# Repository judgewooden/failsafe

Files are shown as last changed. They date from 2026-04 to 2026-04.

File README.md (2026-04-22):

failsafe
========

## Synopsis

Failsafe is a project to determine if water is still flowing in a closed water loop for computer cooling. If the water is not flowing it will cut the power to the pump and computers. The computers are cooled with an external radiator and pump which is outside the house. Since these systems are far apart an Arduino monitors the flow to ensure that pumps will not run dry or there is no electric short when there is a water leak or an unknown incident.

Inside the house each computer is split into its own water loop via a manifold. Using flowmeters for each loop an http server display the flow-per-second so that the manifold valves could be adjusted manually. The data is also made available as JSON via rest for an external monitoring software solution running on a seperate Raspberry Pi.

## Code

As the project progressed more features got added:
- Arduino_email: Monitors a single water loop and send an email when the circuit breakers is activated.
- Arduino_dual: Monitors multiple water loops, expose data in rest for external monitoring and removed email.
- Arduino_nvram: Monitors multiple water loops and make it possible to service a computer. It stores the last config in nvram, so when it restarts it will remember what loops needs to be monitored.

## Motivation

The computers are on 24/7 and with water cooling things sometimes go wrong. But it was also an opportunity to learn more about hardware programming and the Arduino.

## Installation

Hardware:

- 1x Arduino
- 1x Arduino Ethernetboard (Duemilanova w/Atmega328)
- 3x water flow meters
- 1x 220v switch

## Circuits

- fritzing = logical circuit drawing
- picture = circuit board (With before pictures)

## Tests

There was several leaks over the years and the failsafe works.

## Example

Below is a sample screen of what you can control via the web server.

- In this example only two loops are active and only loop-0 is being monitored.
- Set minutes. Allows you to temporary disable monitoring. This is needed when you service the outside loop (radiator) or when you start the system. It will countdown and eventually reset to monitoring mode.
- Change ON/OFF per loop. This allows you to enable/disable monitoring per loop. Useful if you service a computer. The eeprom-code option allow you to save this setting into eeprom.

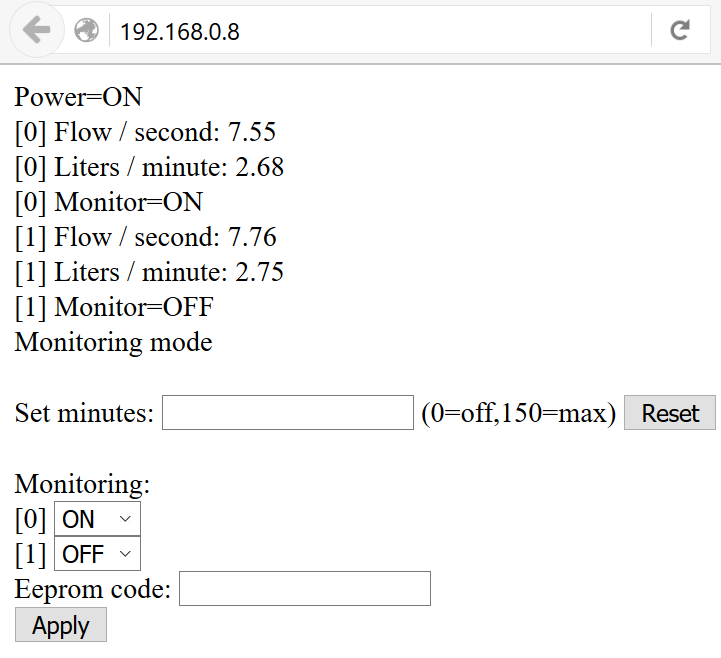
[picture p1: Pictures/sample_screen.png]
sample screen


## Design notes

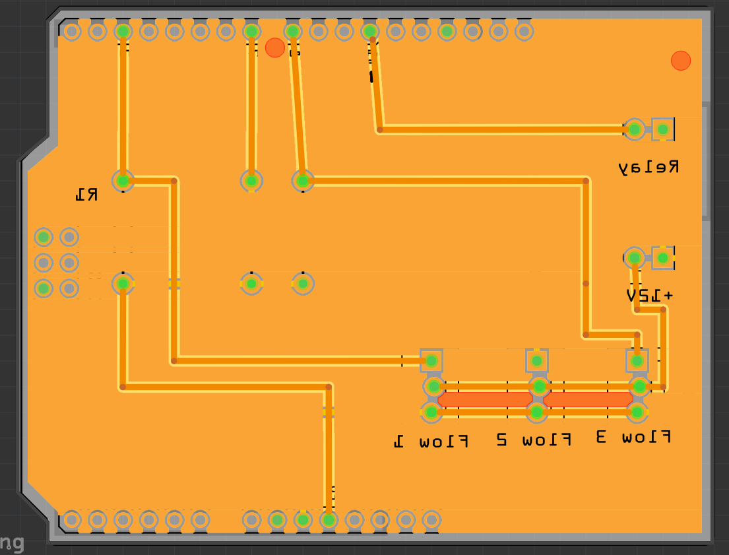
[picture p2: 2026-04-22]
Pictures/A_pcb_back.png

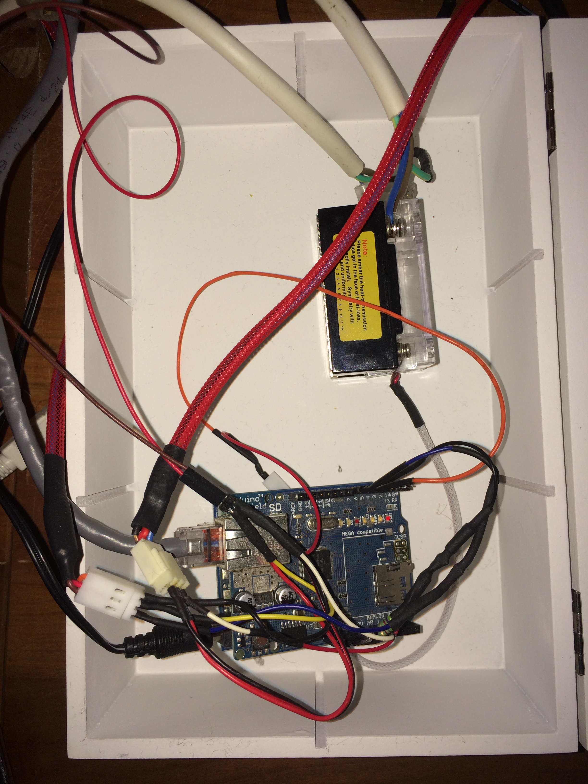
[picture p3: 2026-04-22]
Pictures/Two_circuits.jpg

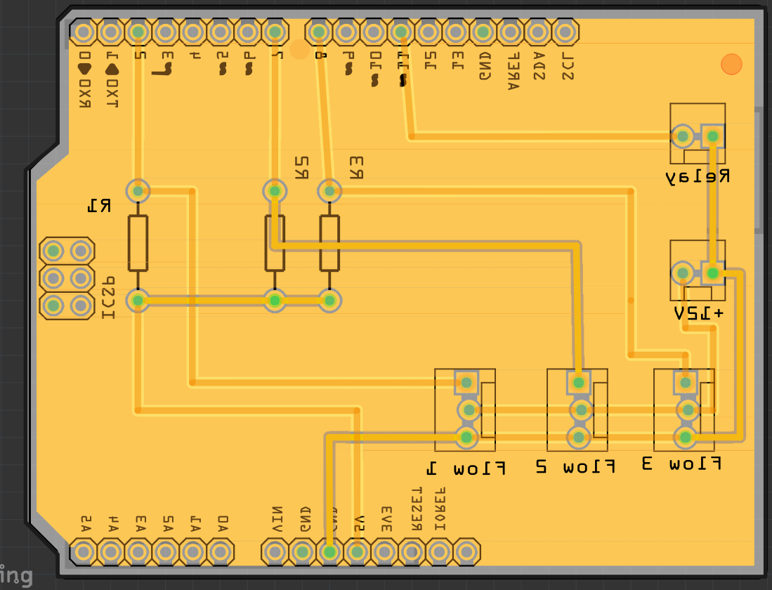
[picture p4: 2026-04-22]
Pictures/A_pcb_front.png

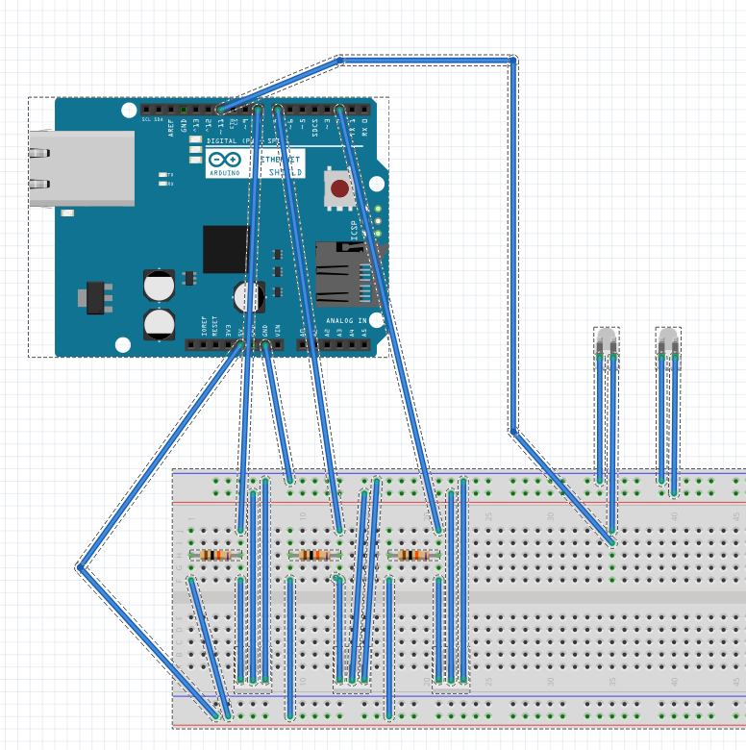
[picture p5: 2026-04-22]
Pictures/A_breadboard.png

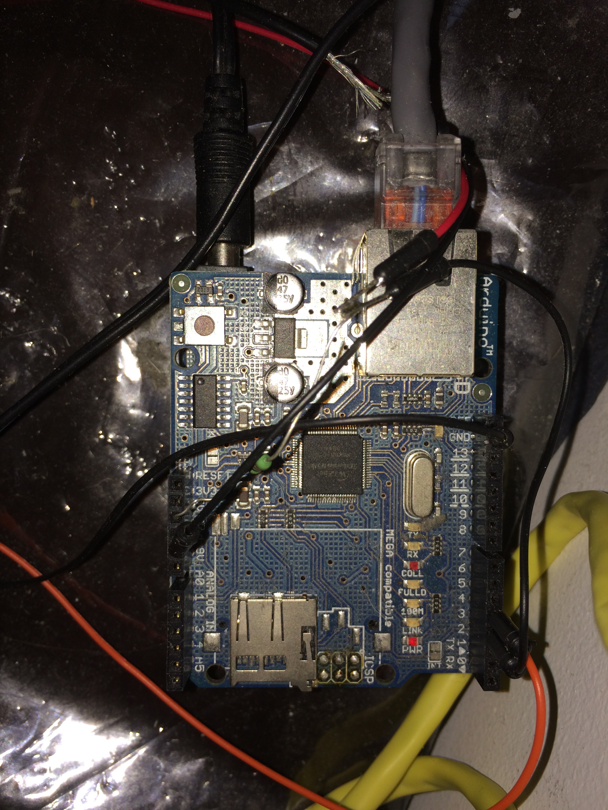
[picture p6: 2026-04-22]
Pictures/Single_circuit.jpg

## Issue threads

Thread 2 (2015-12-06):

When no flow, last readings is not updated

judgewooden, 2015-12-06:
Readings are not updated, where there is no flow. Although failsafe has been activated the web interface can still show the wrong last values

Closed 2016-02-14.

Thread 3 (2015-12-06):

Create a second flow meters to monitor

judgewooden, 2015-12-06:
First create an overflow failsafe with two reporting XML outputs and one website.

Later considering adding a failsafe OVERRIDE mode per sensor.

Closed 2016-02-14.

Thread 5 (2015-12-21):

Send a notification to server a httlp server on failsafe

judgewooden, 2015-12-21:
When the failsafe kicks in, sent a http GET message with parameters about the current status and config after the power is switched off.

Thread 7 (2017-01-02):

Issues with JSON array

judgewooden, 2017-01-02:
Sometime the array is not ending correct. Notice comma after last field in example below.

{"Power":1,"Loop":0,"Mode":2,"ValuesReset":0,"FlowPerSecond":3.08,"LitersPerSecond":1.09,"OverrideTime":0,"CurrentTime":3958098307,"data":[3958090244,3958090569,3958090892,3958091210,3958091533,3958091862,3958092185,3958092507,3958092830,3958093155,3958093483,3958093810,3958094132,3958094453,3958094789,3958095119,3958095442,3958095766,3958096129,3958096413,3958096741,3958097063,3958097385,3958097714,3958098038,]}

judgewooden, 2020-02-17:
It has now been running for 2 years. The error is only for users that extract the data as JSON. Unfortunately a user that extracts JSON needs to check for this comma, before parsing it.

Closed 2020-02-17.

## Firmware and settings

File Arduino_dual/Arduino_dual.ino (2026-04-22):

#include "Ethernet.h"
#include <SPI.h>

// Upload to Arduin Duemilanova w/ Atmega328

#define DEBUG 1

int debugflow = 1;                     // Are we debugging flow via serial interface
int debughttp = 1;                     // Are we debugging http via serial interfaces

const int numCircuits = 2;             // number of water sensors connected
const int numReadings = 25;            // number of pulses to check for flow calculation

int pin_input[] = {5, 7};              // On what pins are the water seonsors connected
double pulses_per_liter[] = {169,492};
                                       // Number of pulses per liter water
int pin_output = 6;                    // On what pin is the circuit breaker connected

long override_time= 120000;             // Give a 2 minute startup
int override_mode = 0;                  // Are we monitoring the flow
int Is_Power_On = 0;                    // Keep the state of the power breaker
int jsonresponse = 0;                   // Should I reply with JSON data on the HTML

int lastpulse[numCircuits];             // Was the last pulse high or low
unsigned long last_pulse_time[numCircuits];
                                        // When was the last pulse
unsigned long readings[numReadings][numCircuits];
                                        // Array to keep pin readings to calculate flow
int index[numCircuits];                 // keep track where we are in the Array
double Pulses_Per_Second[numCircuits];  // The calculated pulses per second
double Liter_per_minute[numCircuits];   // The calculated liters per minute
int valuesreset[numCircuits];           // Indicate if values are reset

unsigned long current_time;             // get the current system time
unsigned long timeout_millisecs = 5000; // Nr of miliseconds of no flow before activating circuit breakers

const double MilliPerSecond = 1000;     // a field to force caculcation as a double
unsigned long report_count = 0;         // the last time that a caulcation for flow was ade
int report_interval = 1000;             // Nr of miliseconds to calculate flow numbers

// Ethernet library configuration
byte mac[] = {
  0xDE, 0xAD, 0xBE, 0xEF, 0xFE, 0xED }; //physical mac address
byte ip[] = {192, 168, 0, 8 };          // ip in lan
byte gateway[] = {192, 168, 0, 1 };     // internet access via router
byte smtp_server[] = {192, 168, 0, 5};  // my-host.com

// HMTL processing variables
EthernetServer server(80);              //server port
String readString = "";                 //string to get incoming data
char c;
char buffer[10];
int dataLength =0;

// Buffer containing processed hmtl data
char data[50];
char datamotor[5];


void setup() {

  for (int z = 0; z < numCircuits; z++) {
    pinMode(pin_input[z], INPUT);
    lastpulse[z]=0;
    last_pulse_time[z]=0;
    index[z]=0;
    valuesreset[z]=0;
  }
  pinMode(pin_output, OUTPUT);

  //attachInterrupt(0, blink, FALLING);
  Serial.begin(9600);

  for (int z = 0; z < numCircuits; z++)
    for (int x = 0; x < numReadings; x++)
      readings[x][z] = 0.0;

  Ethernet.begin(mac, ip, gateway); //start Ethernet
  delay(1000);

  digitalWrite(pin_output, HIGH);
  Is_Power_On = 1;

  Serial.print("POWER:");
  Serial.println(Is_Power_On);

  if(override_time>0)
    override_mode=1;
  else
    override_mode=0;

}

void loop() {

  // read the input pin:
  for (int z = 0; z < numCircuits; z++) {
    int buttonState = digitalRead(pin_input[z]);
    //Serial.print(z);
    //Serial.print(">");
    //Serial.print(buttonState);
    //Serial.print(" ");

    // count pulses in the loop
    if ( buttonState != lastpulse[z] ) {
      lastpulse[z] = buttonState;

      if(lastpulse[z]) {
        last_pulse_time[z]=millis();

        readings[index[z]][z]=last_pulse_time[z];
        index[z]++;
        if (index[z] >= numReadings)
          index[z]=0;
      }
    }
  }

  current_time = millis();

  // check if the power should switch off  (for now only check first loop)
  //  for (int z = 0; z < numCircuits; z++) {
    if(current_time > (timeout_millisecs + last_pulse_time[0]) ) {
      if (debugflow) Serial.print("[");
      if (debugflow) Serial.print(0);
      if (debugflow) Serial.print("] ");
      if (debugflow) Serial.print("ALERT. No flow for ");
      if (debugflow) Serial.print(timeout_millisecs);
      if (debugflow) Serial.print(" milliseconds. ");
      if (override_mode) {
        if (debugflow) Serial.println("KILL SIGNAL SKIPPED)!");
      }
      else {
        digitalWrite(pin_output, LOW);
        if (debugflow) Serial.println("SEND KILL SIGNAL");
        if (Is_Power_On) {
          Is_Power_On = 0;
        }
      }
    }
  //}

  // report some interersting things
  if( (current_time / report_interval) > report_count) {
    if (debugflow) Serial.print("Time: ");
    if (debugflow) Serial.println(current_time);

    for (int z = 0; z < numCircuits; z++) {

      // Show the average for last readings
      double total = 0;
      int looper;

      if ( index[z] != 0)
        total +=  readings[0][z] - readings[numReadings - 1][z];

      for ( looper = 1; looper < index[z]; looper++)
        total += readings[looper][z] - readings[looper - 1][z];

      for ( looper = index[z] + 1; looper < numReadings; looper++)
        total += readings[looper][z] - readings[looper - 1][z];

      Pulses_Per_Second[z] = MilliPerSecond / (total / (numReadings-1));

      if (debugflow) Serial.print("[");
      if (debugflow) Serial.print(z);
      if (debugflow) Serial.print("] ");
      if (debugflow) Serial.print("Average : ");
      if (debugflow) Serial.println(Pulses_Per_Second[z]);

      Liter_per_minute[z] = Pulses_Per_Second[z] * 60 / pulses_per_liter[z];
      if (debugflow) Serial.print("[");
      if (debugflow) Serial.print(z);
      if (debugflow) Serial.print("] ");
      if (debugflow) Serial.print("Liter /pm: ");
      if (debugflow) Serial.println(Liter_per_minute[z]);
    }

    if (debugflow) Serial.print("    POWER:");
    if (debugflow) Serial.println(Is_Power_On);

    // countdown the time for override mode
    if(override_mode) {
      override_time -= report_interval;
      if (debugflow) Serial.print("    IN OVERRIDE MODE time left: ");
      if (debugflow) Serial.print(override_time);
      if (debugflow) Serial.println(" milliseconds ");
      if (override_time<0) {
        override_mode=0;
        override_time=0;
      }
    }

    // if no flow for double the timeout period blank all flow values
    for (int z = 0; z < numCircuits; z++) {
      if(current_time > ((2 * timeout_millisecs) + last_pulse_time[z]) ) {
        for (int i = 0; i < numReadings; i++) {
          readings[i][z] = 0.0;
        }
        valuesreset[z]=1;
        if (debugflow) Serial.print("[");
        if (debugflow) Serial.print(z);
        if (debugflow) Serial.print("] ");
        if (debugflow) Serial.println(" (values reset)");
      }
      else {
        if (valuesreset[z]) {
          if((current_time - last_pulse_time[z]) < (2 * timeout_millisecs) ) {
            valuesreset[z]=0;
            if (debugflow) Serial.print("[");
            if (debugflow) Serial.print(z);
            if (debugflow) Serial.print("] ");
            if (debugflow) Serial.println(" (flow detected)");
          }
        }
      }
    }

    report_count++;
  }

  handle_http();

}

void reset_http_vals() {
  // Reinitializing variables
  readString =""; // Reinitialize String
  for (int i=0; i<10; i++)
  {
    buffer[i] = '\0';
  }
  for (int i=0; i<50; i++)
  {
    data[i] = '\0';
  }
  for (int i=0; i<5; i++)
  {
    datamotor[i] = '\0';
  }
  dataLength =0;
}

void handle_http() {
  EthernetClient client = server.available();

  if (client) {
    while (client.connected()) {
      while (client.available()) { // Receive client data

        if (debughttp) Serial.print(".");
        c = client.read(); //read char by char HTTP request
        readString +=c;
        //Serial.print(c); //output chars to serial port

        // If first request upon connexion, the 3 first characters will be "GET"
        // If "GET" is caught, skip the request info
        if( readString.equals("GET")) {
          if (debughttp) Serial.println("");
          c = client.read();
          c = client.read();
          c = client.read();
          if (c == 'X' || c == '1' )
            jsonresponse=1;
          else {
            if ((c == 'Y' || c == '2') && numCircuits > 1)
              jsonresponse=2;
            else {
              if ((c == 'Z' || c =='3') && numCircuits > 2)
                jsonresponse=3;
              else
                jsonresponse=0;
            }
          }
          if (debughttp) Serial.print("JSON=");
          if (debughttp) Serial.print(jsonresponse);
          if (debughttp) Serial.println(", GET");
          break;
        }

        // Otherwise, if the request contains data,
        // the first characters will be "POST"
        // We then skip the request header and this "if" becomes our main function
        if( readString.equals("POST")) {
          if (debughttp) Serial.println("");
          if (debughttp) Serial.println("POST");
          // 320 is arbitrary. The actual length that has to be skipped depends on
          // several user settings ( browser, language, addons...)
          // the skipped length has not to be too long to skip relevant data
          // and not to short to waste computing time
          for(int i=0; i<320; i++) {
            c = client.read();
            if (debughttp) Serial.print(c); // UNCOMMENT FOR DEBUG
          }

          //Searches for "Length: "
          while(c != 'L') {
            c = client.read();
            if (debughttp) Serial.print(c); // UNCOMMENT FOR DEBUG
          }

          // Skip "Length: "
          for (int i=0; i<7; i++)
          {
            c = client.read();
            if (debughttp) Serial.print(c); // UNCOMMENT FOR DEBUG
          }

          // Read the data package length
          readString="";
          c = client.read();

          while(c != '\n')
          {
            readString += c;
            if (debughttp) Serial.print(c);
            c = client.read();
          }
          // convert data read from String to int
          readString.toCharArray(buffer, readString.length());
          dataLength = atoi(buffer);
          if (debughttp) Serial.println("");
          if (debughttp) Serial.print("dataLength: ");
          if (debughttp) Serial.println(dataLength);

          // gets DATA
          client.read(); // skips additional newline
          client.read();
          for (int i=0; i<dataLength; i++) {
            data[i] = client.read();
          }

          if (debughttp) Serial.println("");
          if (debughttp) Serial.print("data: ");
          if (debughttp) Serial.println(data);

          readString ="";
          int i = 0;
          while(data[i] != '=')
            i++;
          i++;

          if (debughttp) Serial.println(data + i);

          override_time = atoi(data + i);
          if (override_time>150)
            override_time = 150;

          override_time *= 60000;
          if (debughttp) Serial.print("Override period: ");
          if (debughttp) Serial.println(override_time);

          if(override_time>0)
            override_mode=1;
          else
            override_mode=0;
        }
      }

      if (jsonresponse) {
        // JSON CODE
        client.println("HTTP/1.1 200 OK");
        client.println("Content-Type: application/json");
        client.println("Connection: close");
        client.println();
        client.print("{\"Power\":");
        client.print(Is_Power_On);
        client.print(",\"Loop\":");
        client.print(jsonresponse-1);
        client.print(",\"ValuesReset\":");
        client.print(valuesreset[jsonresponse-1]);
        client.print(",\"FlowPerSecond\":");
        client.print(Pulses_Per_Second[jsonresponse-1]);
        client.print(",\"LitersPerSecond\":");
        client.print(Liter_per_minute[jsonresponse-1]);
        client.print(",\"OverrideTime\":");
        client.print(override_time);
        client.print(",\"CurrentTime\":");
        client.print(current_time);
        client.print(",\"data\":[");

        int looper;
        for ( looper = index[jsonresponse-1]; looper < numReadings; looper++) {
          client.print(readings[looper][jsonresponse-1]);
          client.print(",");
        }

        for ( looper = 0; looper < index[jsonresponse-1]; looper++) {
          client.print(readings[looper][jsonresponse-1]);
          if (looper < (index[jsonresponse-1]-1))
            client.print(",");
        }

        client.println("]}");
        client.println("");

      }
      else {
        // HTML CODE
        client.println("<!DOCTYPE html>");
        //        client.println("HTTP/1.1 200 OK");
        //        client.println("<meta http-equiv=\"Content-Type\" content=\"text/html;charset=ISO-8859-8\">");
        client.print("<meta http-equiv=\"refresh\" content=\"");
        client.print(report_interval/1000*5);
        client.println("\">");
        client.println("<html>");
        //Serial.print(report_interval/1000*5);

        if (Is_Power_On)
          client.print("The power is ON");
        else
          client.print("The power is OFF");

        for (int z = 0; z < numCircuits; z++) {
          client.print("<br>[");
          client.print(z);
          client.print("] ");
          client.print("Flow per second: ");
          client.print(Pulses_Per_Second[z]);

          if (valuesreset[z]>=1)
            client.print(" (values reset)");
          client.print("<br>[");
          client.print(z);
          client.print("] ");
          client.print("Liters per minute: ");
          client.print(Liter_per_minute[z]);
          if (valuesreset[z]>=1)
            client.print(" (values reset)");
        }

        if (override_time>0) {
          client.print("<br>Override mode, time remaining: ");
          client.print(override_time / 1000 / 60);
          client.print(":");
          int remainder = (override_time / 1000) % 60;
          if (remainder < 10)
            client.print("0");
          client.print(remainder);
          client.print("<br><br>*** WARNING - OVERRIDE MODE WILL NOT DISABLE POWER ***");
        }
        else
          client.print("<br>Monitoring mode");
        client.print("<br> ");

        client.println("<br><form name=input method=post>Set override minutes : ");
        client.println("<input type=\"text\" value=\"");
        //     client.print(override_time);
        client.print("\" name=\"override_time\" />");
        client.print(" (0=off,150=max) ");
        client.println("<input type=\"submit\" value=\"Reset\" />");
        client.println("</form> <br /> ");

        client.println("</html>");
      }
      client.stop();
    }
  }

  reset_http_vals();
}
